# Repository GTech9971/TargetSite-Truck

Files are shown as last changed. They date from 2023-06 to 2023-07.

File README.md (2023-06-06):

# TargetSite-Truck

 ionic/react iosからBlueooth経由でデータを受信し、モータを操作することでラジコンを動かす

## マイコン PIC16F1827

[datasheet](datasheet/pic16f1827.pdf)

## HM-10

BLE規格のモジュール

| サービスUUID | キャラUUID |
| --- | --- |
| FFE0 | FFE1 |

[datasheet](datasheet/DSD%20TECH%20HM-10%20datasheet.pdf)

### USART

RX = RB1
TX = RB2

ピンを全てデジタルに設定

```
ANSELA = 0x00;
ANSELB = 0x00;
```

RXピンを入力モードに設定

```
TRISA = 0x00;
TRISB = 0x02;
```

RX,TXを有効化

```
TXSTA = 0x20;
RCSTA = 0x90;
```

通信設定

```
//16bit
BAUDCON = 0x08;

//9600bit mode
SPBGR = 51;
```

データ送信

```
void send(unsigned char data){
    while(!TXSTAbits.TRMT);
    TXREG = data;
}

```

### 割り込み

割り込み有効化

```
//interrupt flg clear
PIR1bits.RCIF = 0;
    
//USART recive interrupt enable
PIE1bits.RCIE = 1;
//peripheral enable
PEIE = 1;
//global enable
GIE = 1;
```

割り込み関数

```
void __interrupt() isr(void){
    if(PIR1bits.RCIF){
        //flg clear
        PIR1bits.RCIF = 0;
        //error
        if((RCSTAbits.OERR) || (RCSTAbits.FERR)){
            RCSTA = 0;
            RCSTA = 0x90;
        }else{
        //not error            
            //RCREGが受信データ
            send(RCREG);
        }
    }
}
```

## TA7291P

モータードライバー
[datasheet](datasheet/ta7291.pdf)

### ファンクション

| IN1 | IN2 | モード |
| --- | --- | --- |
| 0 | 0 | ストップ |
| 1 | 0 | 前進 |
| 0 | 1 | 後退 |
| 1 | 1 | ブレーキ |

### CCP(PWMモード)

PWM有効化 CCP3

```
//pwm initialize
// CCP3M PWM; DC3B 3; 
CCP3CON = 0x3C;    
// CCPR3L 127; 
CCPR3L = 0x7F;    
// CCPR3H 0; 
CCPR3H = 0x00;    
// Selecting Timer 2
CCPTMRS0bits.C3TSEL = 0x0;
    
//timer2 initialize
// PR2 255; 
PR2 = 0xFF;
// TMR2 0; 
TMR2 = 0x00;
// Clearing IF flag.
PIR1bits.TMR2IF = 0;
// T2CKPS 1:1; T2OUTPS 1:1; TMR2ON on; 
T2CON = 0x04;
```

## データ仕様

| bit7 | bit6 | bit5 |  bit4 | bit3 | bit2 | bit1 | bit0 |
| :--: | :--: | :--: | :-----: | :--: | :--: | :--: | :--: |
|  > | CMD  |  > | INC/DEC |  > | SPD  | | |

### CMD

トラックへの命令
| bit7 | bit6 |  モード  |
| :--: | :--: | :---: |
|  0 |  0 | 停止 |
|  1 |  0 | 前進 |
|  0 |  1 | 後退 |
|  1 |  1 | ブレーキ |

### INC/DEC

- INC

    現在のスピードからSPDの値に増加していく

- DEC
    現在のスピードから徐々に減少していく

| bit5 | bit4 | モード |
| :--: | :--: | :----: |
|  0 |  0 |  通常  |
|  0 |  1 |  INC |
|  1 |  0 |  DEC |

### SPD

モーターのスピードを設定する(10進数で0~10までの値)
| bit3 | bit2 | bit1 | bit0 |
| ---- | ---- | ---- | ---- |

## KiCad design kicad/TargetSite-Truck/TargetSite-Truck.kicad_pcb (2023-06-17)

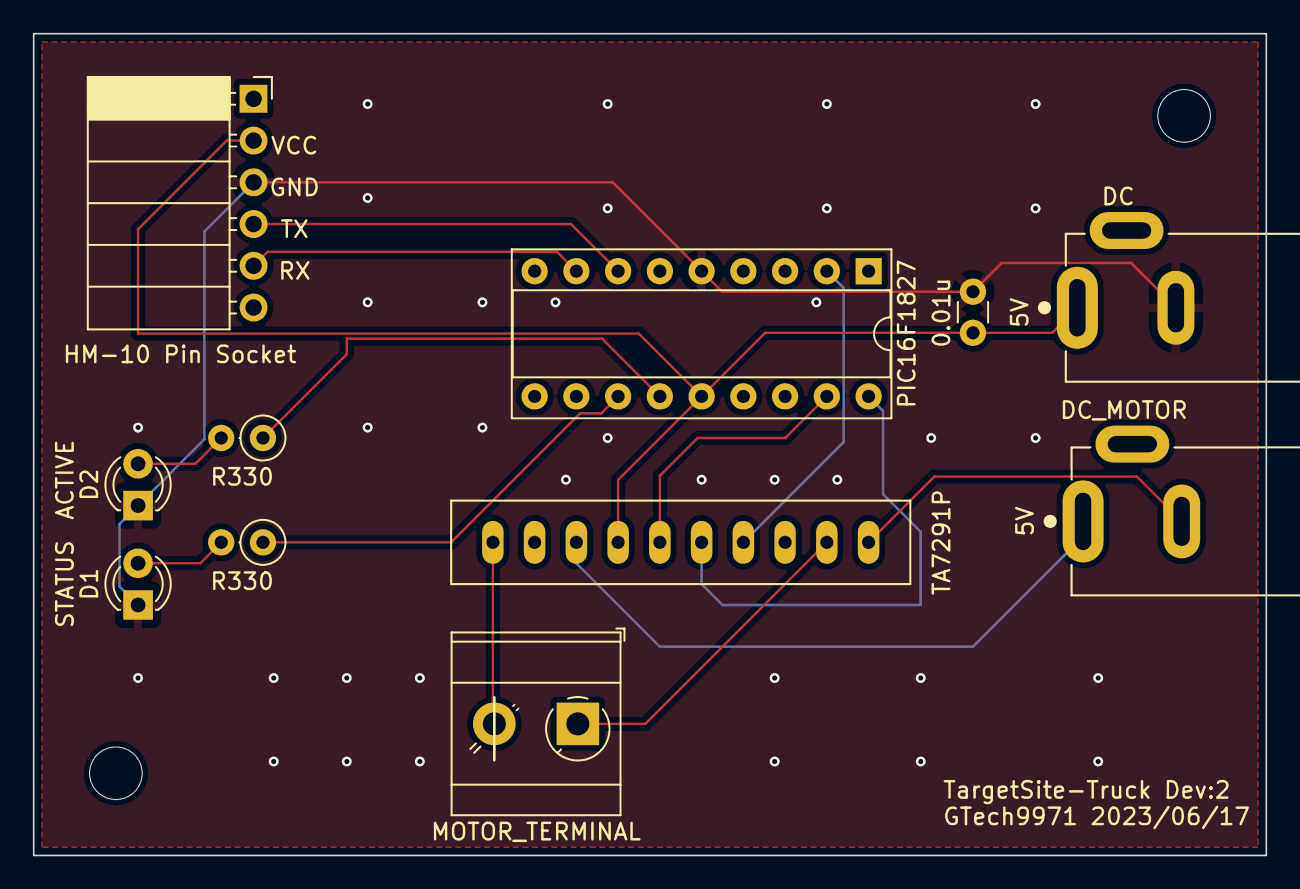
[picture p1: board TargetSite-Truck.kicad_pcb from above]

Board: 2 copper layers, 75.0 x 50.0 mm, 13 parts (0 on the bottom side), 15 nets.

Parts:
0.01u: 0.01u; C_Disc_D3.0mm_W1.6mm_P2.50mm
D1: LED_STATUS; LED_D3.0mm
D2: LED_ACTIVATE; LED_D3.0mm
DC: 5v; CUI_PJ-002AH
DC_MOTOR: 9v; CUI_PJ-002AH
HM-10 Pin Socket: HM10; PinSocket_1x06_P2.54mm_Horizontal
MH1, MH2: MountingHole_3.2mm_M3
MOTOR_TERMINAL: Motor_DC; TerminalBlock_MetzConnect_Type073_RT02602HBLU_1x02_P5.08mm_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
PIC16F1827: PIC16F1827-E/P; DIP-18_W7.62mm_Socket
R330, R330#2: R330; R_Axial_DIN0207_L6.3mm_D2.5mm_P2.54mm_Vertical
TA7291P: TA7291P; HSIP10

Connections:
DC_GND: DC_MOTOR.2, TA7291P.1 (GND)
DC_VCC: DC_MOTOR.1, TA7291P.8 (VS)
Driver_IN1: PIC16F1827.18 (RA1/AN1/CPS1/C12IN1-/~SS2), TA7291P.5 (IN1)
Driver_IN2: PIC16F1827.17 (RA0/AN0/CPS0/C12IN0-/SDO2), TA7291P.6 (IN2)
Driver_Ref: PIC16F1827.2 (RA3/AN3/CPS3/C12IN3-/C1IN+/VREF+/C1OUT/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), TA7291P.4 (VREF)
GND: 0.01u.1, D1.1 (K), D2.1 (K), DC.2, HM-10 Pin Socket.3, PIC16F1827.5 (VSS)
HM10_RX: HM-10 Pin Socket.5, PIC16F1827.8 (RB2/AN10/CPS10/MDMIN/TX/CK/RX/DT/SDA2/S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)
HM10_TX: HM-10 Pin Socket.4, PIC16F1827.7 (RB1/AN11/CPS11/RX/DT/SDA1/SDI1)
Motor_IN1: MOTOR_TERMINAL.1 (+), TA7291P.2 (OUT1)
Motor_IN2: MOTOR_TERMINAL.2 (-), TA7291P.10 (OUT2)
unnamed: D1.2 (A), R330.2
unnamed: D2.2 (A), R330#2.2
unnamed: PIC16F1827.12 (RB6/AN5/CPS5/T1CKI/T1OSI/P1C/CCP2/P2A/I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), R330.1
unnamed: PIC16F1827.13 (RB7/AN6/CPS6/T1OSO/P1D/P2B/MDCIN1/ICSPD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), R330#2.1
VCC: 0.01u.2, DC.1, HM-10 Pin Socket.2, PIC16F1827.14 (VDD), TA7291P.7 (VCC)

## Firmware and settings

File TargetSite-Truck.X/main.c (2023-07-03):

#include "mcc_generated_files/mcc.h"
#include <stdbool.h>
#include "./HM-10.h"
#include "./Led.h"
#include "TruckCommand.h"
#include "Truck.h"

Truck truck;
bool status_led_flag = false;

void main(void)
{
    // initialize the device
    SYSTEM_Initialize();    
    
    initialize_hm10();
        
    Led led = {0x80, 0x40};
    initialize_led(&led);
    //起動用LED点灯
    blink_activate_led(&led);
    
    //ステータス用LED点灯
    blink_status_led(&led);
    
    
    /** input1, input2, vrefpin, speed */
    TA7291P driver = {0x01, 0x02, 0x08, 0x00};
    initialize(&driver);
    
    
    
    //トラック初期化
//    truck.driver = &driver;
//    truck.led = &led;
   
    uint16_t count = 0;

    //pwmの値が低いとモーターが動かないある程度の値は必要
    while (1)
    {
        //forward(&driver, 1000);
        if(count == 1023){
            count = 0;            
            __delay_ms(1000);            
        }
        
        forward(&driver, count);        
        
                
        __delay_ms(10);
        
        count++;
    }
    
//    while (1)
//    {
//        forward(&driver, 1000);
        // DEBUG
//        if(status_led_flag == false){
//            high_status_led(truck.led);
//            status_led_flag = true;
//        }else{
//            low_status_led(truck.led);
//            status_led_flag = false;
//        }
//        uint8_t data = 0x00;
//        TruckCommand truck_cmd = {STOP, NONE, 0};
//        create_command(data, &truck_cmd);
//            
//        execute_command(&truck, &truck_cmd);
    //}
}

/**
 * interrupt func
 */
void __interrupt() isr(void){
    if(PIR1bits.RCIF){
        //flg clear
        PIR1bits.RCIF = 0;
        //error
        if((RCSTAbits.OERR) || (RCSTAbits.FERR)){
            RCSTA = 0;
            RCSTA = 0x90;
        }else{
            //not error         
            if(status_led_flag == false){
                high_status_led(truck.led);
                status_led_flag = true;
            }else{
                low_status_led(truck.led);
                status_led_flag = false;
            }
            uint8_t data = RCREG;
            TruckCommand truck_cmd = {STOP, NONE, 0};
            create_command(data, &truck_cmd);
            
            execute_command(&truck, &truck_cmd);
        }
    }
}

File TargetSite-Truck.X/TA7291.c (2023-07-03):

#include "TA7291P.h"

static void set_input1_pin_low(TA7291P *p){
    LATA &= ~p->input1_pin;
}
static void set_input1_pin_high(TA7291P *p){
    LATA |= p->input1_pin;
}

static void set_input2_pin_low(TA7291P *p){
    LATA &= ~p->input2_pin;
}
static void set_input2_pin_high(TA7291P *p){
    LATA |= p->input2_pin;
}

/**
 * ピンのANSEL,TRISの設定
 * @param p
 */
void initialize(TA7291P *p){    
    //input1_pin
    //input2_pin
    //vref_pin
    //出力設定(input:1, output:0)
    TRISA &= ~p->input1_pin;
    TRISA &= ~p->input2_pin;
    //TRISA &= ~p->vref_pin;
    
    //vrefピンのアナログ設定(analog:1, digital:0)
    //ANSELA |= p->vref_pin;
    
//    //PWM初期化
//    // CCP3M PWM; DC3B 3; 
//	CCP3CON = 0x3C;    
//	// CCPR3L 127; 
//	CCPR3L = 0x7F;    
//	// CCPR3H 0; 
//	CCPR3H = 0x00;    
//	// Selecting Timer 2
//	CCPTMRS0bits.C3TSEL = 0x0;
//    
//    //Timer2 初期化
//    // PR2 255; 
//    PR2 = 0xFF;
//    // TMR2 0; 
//    TMR2 = 0x00;
//    // Clearing IF flag.
//    PIR1bits.TMR2IF = 0;
//    // T2CKPS 1:1; T2OUTPS 1:1; TMR2ON on; 
//    T2CON = 0x04;
    
    stop(p);
}

/**
 * モーターのスピードを設定する
 * @param p
 * @param speed
 */
void set_speed(TA7291P *p, uint16_t speed){
    p->speed = speed;
    pwm_load_duty_value(p->speed);    
}

/**
 * pwmのデューティー比を変更する
 * @param duty_value 0~1023
 */
static void pwm_load_duty_value(uint16_t duty_value){
    // Writing to 8 MSBs of pwm duty cycle in CCPRL register
    CCPR3L = ((duty_value & 0x03FC)>>2);
    
   // Writing to 2 LSBs of pwm duty cycle in CCPCON register
    CCP3CON = ((uint8_t)(CCP3CON & 0xCF) | ((duty_value & 0x0003)<<4));
}

/**
 * モーター停止
 * @param p
 */
void stop(TA7291P *p){
    set_input1_pin_low(p);
    set_input2_pin_low(p);
    
    //set_speed(p, 0);
}

/**
 * モーター直進
 * @param p
 * @param value
 */
void forward(TA7291P *p, uint16_t value){
    set_input1_pin_high(p);
    set_input2_pin_low(p);
    
    //set_speed(p, value);
}

/**
 * モーター後退
 * @param p
 * @param value
 */
void back(TA7291P *p, uint16_t value){    
    set_input1_pin_low(p);
    set_input2_pin_high(p);
    
    //set_speed(p, value);
}

/**
 * モーターブレーキ
 * @param p
 */
void brake(TA7291P *p){
    set_input1_pin_high(p);
    set_input2_pin_high(p);
}

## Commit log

2023-05-06 回路図、フットプリント作成
    [TargetSite-Truck.kicad_pcb, TargetSite-Truck.kicad_sch]
2023-05-07 プログラムプロジェクトを追加
2023-05-26 回路図の作成、PCBの作成
    [TargetSite-Truck.kicad_pcb, TargetSite-Truck.kicad_sch]
2023-05-27 ガーバーデータの作成
    [TargetSite-Truck-B_Cu.gbl, TargetSite-Truck-B_Mask.gbs, TargetSite-Truck-B_Silkscreen.gbo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]
2023-06-06 データ仕様を記載
2023-06-06 データシートの追加 データ仕様の修正
2023-06-06 ドライバーコードを実装 Ledを実装 HM10の初期化を実装 トラックコマンドを実装
2023-06-07 コマンドの処理をいくつか実装 エラーが出る状態
2023-06-09 プログラムのバグを修正 デバックモードでテスト実施
2023-06-10 ドライバーのピンアサインを修正 PWM、Timerの初期化を忘れていたのでドライバーの初期化時に設定
2023-06-11 発注した基板でモータが動作したことを確認。 動かなかった原因は以下 PWM・タイマー2の有効化ができていなかった。 電源起動時に入力1,2をLにしていなかった。 forward関数にバグがあった。テストプロジェクトもバグがあるので動作しない。
2023-06-17 回路基板設計修正
    RA0、RA1の配線を引き直した
    ターミナルのピッチサイズを5.08mmに変更
    [TargetSite-Truck-B_Cu.gbl, TargetSite-Truck-B_Mask.gbs, TargetSite-Truck-B_Silkscreen.gbo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]
2023-07-03 pwm制御をオフにした
